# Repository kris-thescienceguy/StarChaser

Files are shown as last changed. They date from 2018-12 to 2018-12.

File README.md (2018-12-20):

# Star Chaser: Automatic Dome Controller

The Star Chaser dome control project was led by Kris Turner as part an upgrade, commissioned by Keele Observatory, in order to improve the functionality of their 24" research, reflector telescope.

Keele Observatory is located in North Staffordshire,  between Manchester and Birmingham on a large estate with extensive woods, lakes and parkland, formerly owned by the Sneyd family. 97% of the university's research is classified as world leading and of international importance, as a result of the 2014 Research Excellence Framework (REF 2014).

The software and digital electronics were produced by **Kris Turner**, who at the time of the project, was an undergraduate physics with chemistry student. The mechanical designs were produced by **Dr James Albinson**. **Alan Bagnell** advised on the design, and safety, of the electrical systems.

*A special mention must be made to the entirety of the Keele Observatory volunteers without who there would be no dome to upgrade.*

## Project Overview ##

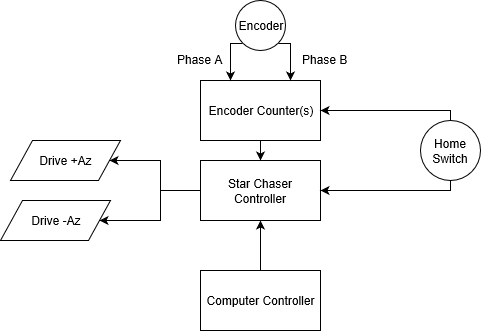
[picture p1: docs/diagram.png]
Schematic diagram of project


## Wiring Specifications ##
The system has several parts which may need to replaced over time so for ease of use a wiring colour chart has been produced. This should be used in conjunction with wiring diagrams provided.

### Pulse Switch ###
There is no doubt that the microcontroller will miss some encoder pulses. It may also count some twice. Whether by gain or loss of pulses it’s likely that with extended use and due to cumulative error the accuracy of the system will decrease over time. In order to prevent this, a zero point was chosen where the microcontroller knows the exact azimuth of the dome. Using a magnet on the dome structure and a fixed reed switch, a pulse is sent to the microcontroller when this zero point is reached.

On this interrupt, the microcontroller resets the pulses counted and hence the azimuth of the dome to a known position. This switch is also polled by the driver software as part of the AtHome subroutine.

| Switch Wire | Extended Cable |
| --- | --- |
| Red | Orange |
| Blue | Blue |

### Encoders ###
In order to accurately determine the position of the dome, two incremental encoders are used, although only one is required and currently configurd. Each encoder has four wires: VCC, GND, A Phase, and B Phase. Phase A and phase B are interchangable but will reverse the direction of the encoder. The encoder phase signals require an external pull-up resistor and although the ATTiny25 microcontroller provides internal pull-ups they do not appear to be strong enough.

#### Encoder A ####
| Encoder Function | Encoder Wire | Extended Cable |
| --- | --- | --- |
| VCC | Red | Orange |
| GND | Black | Blue |
| Phase A | Green | Green |
| Phase B | White | Brown |

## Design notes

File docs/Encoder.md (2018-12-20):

# Star Chaser: Automatic Dome Controller
## Encoder Circuit ##

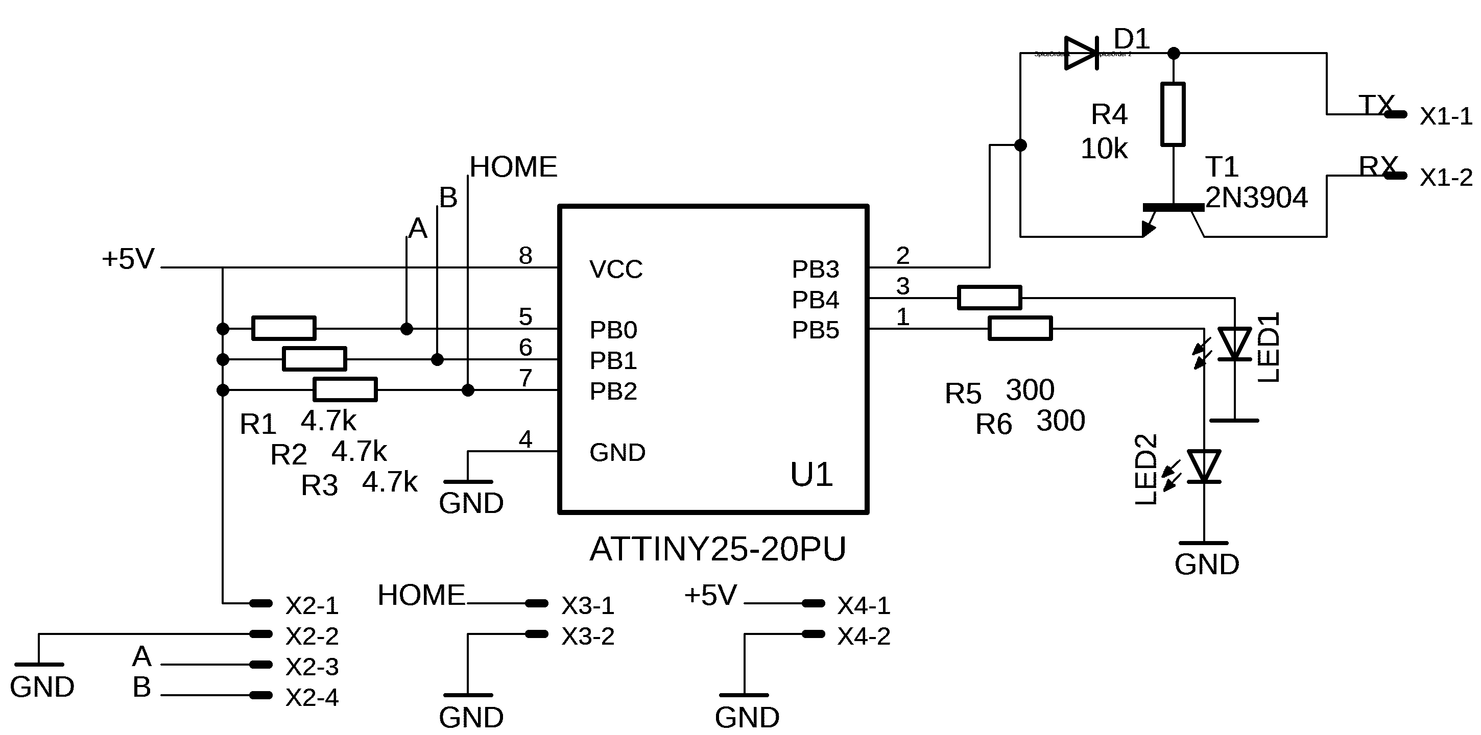
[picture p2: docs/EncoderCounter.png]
Electronic circuit schematic for counting encoder pulses


The encoder circuit is responsible for recording the two 90° out of phase pulses from the rotary encoder. The square waveform, shown below, is measured by the ATTiny25 pins P0 and P1.

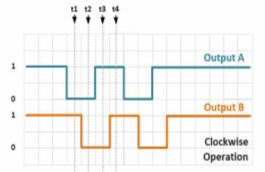
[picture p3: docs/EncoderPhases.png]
Electronic circuit schematic for counting encoder pulses


The encoder circuit is simple, but powerful due to its modular nature. The ATTiny25 is powered from a regulated 5V power bus. Each encoder phase is pulled up through a 4.7k resistor to 5V as is required by an open-collector encoder.

The pros and cons of this is discussed over at CUI Inc https://www.cui.com/blog/comparison-of-common-encoder-output-signals.

The third input, the home switch, is attached to P2 configured as an external interrupt. Again this pin is pulled high by a 4.7k resistor which is grounded by a reed switch in the presence of a magnetic field. This falling edge triggers an interrupt on the ATTiny25 which resets the pulse count to zero.

The board communicates with the controller chip using a software half-duplex serial UART based on a design by Ralph Doncaster which allows only one pin on the ATTiny to be used to both send and receive data. The library compiles to only 62 bytes of memory which is perfect due to the limited memory available on the microcontroller. A more indepth description of the circuit is available from http://nerdralph.blogspot.com/2014/01/avr-half-duplex-software-uart.html.

One status LED's indicate that the dome is moving as measured by the encoders.

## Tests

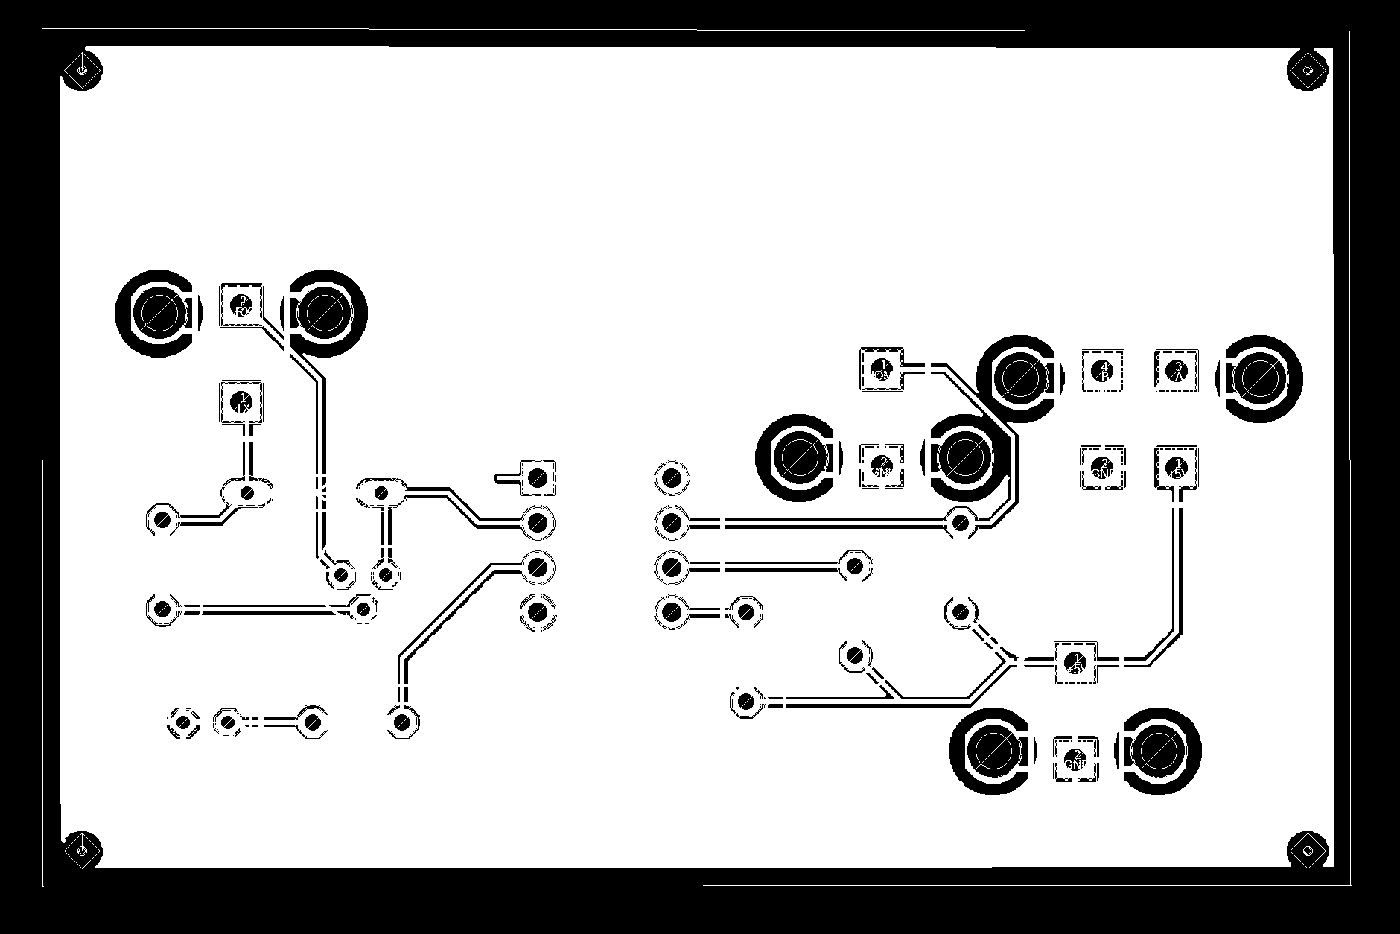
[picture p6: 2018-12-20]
Measurement/PCB.png

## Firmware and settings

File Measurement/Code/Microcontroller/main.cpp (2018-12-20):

/*
 * EEPROM_Dump.cpp
 *
 * Created: 18/12/2018 16:23:59
 * Author : krist
 */ 
#define F_CPU 1000000UL

#include <avr/io.h>
#include <util/delay.h>
#include <avr/interrupt.h>
#include "BasicSerial3.h"

/*
* Pin Definitions
*
* P0 Phase A
* P1 Phase B
* P2 Home
* P3 Serial
* P4 Movement LED
* P5 Reset
*
*/

const signed int encoderDirections[] = {0, -1, 1, 0, 1, 0, 0, -1, -1, 0, 0, 1, 0, 1, -1, 0};
volatile long encCount = 0;
volatile int noMovement = 0;

int main(void)
{
	DDRB = (1 << 3 ); // DDRB = 0011 1000
	PORTB |= (7 << 3); // Flash LEDs (sets P4 to pull up resistor)
	
	bool waitingForStartByte = true;
	
	while (waitingForStartByte){
		if (RxByte() == 's'){
			waitingForStartByte = false;
		}
	}
	
	PORTB &= (0 << 0); // PORTB = 0000 0000 to set pull up resistors off, and set all outputs to zero
	
	GIMSK |= (1 << 5);     // turns on pin change interrupts by setting bit 5 of GIMSK to 1
	GIMSK |= (1 << 6);   // turns on external interrupts
	PCMSK |= (3 << 0);   // set pin change interrupts on pins 0 and 1. Decimal 3 = Binary 11

	/*
	MCUCR Register: ISC0[1:0]: Interrupt Sense Control 0 Bit 1 and Bit 0
	0 0 The low level of INT0 generates an interrupt request.
	0 1 Any logical change on INT0 generates an interrupt request.
	1 0 The falling edge of INT0 generates an interrupt request. <=== This is what we want.
	1 1 The rising edge of INT0 generates an interrupt request.
	*/
	
	MCUCR |= (1 << 1);
	MCUCR &= ~(1 << 0);

	sei();                     // turn on interrupts

	
    /* Replace with your application code */
	
    while (1) 
    {
		//home = ((PINB >> 3) & 1); // Get state of home pin (shifts to LSB and then sets the rest of the array to 0)
		//encCount = encCount * home; // Home is default at 1 until pulled to ground by pin.
		noMovement += 1;
		
		if (noMovement > 5000){
			PORTB &= ~(1 << 4);	
		}
		
		// Transmit value out
		int numberOfBytes = (encCount / 255) + 1;
		for (int byteIndex = 0; byteIndex < numberOfBytes; byteIndex++)	{
			int shiftIndex = (numberOfBytes - byteIndex - 1)*8;
			int transmitByte = (encCount >> shiftIndex) & 255; // Ensures only first 8 bits have value
			TxByte(transmitByte);
		}
		TxByte('#');
    }
}

/* Pin Change Interrupts */
ISR (PCINT0_vect) {
	static unsigned int oldEncoderState = 0;
	
	oldEncoderState <<= 2;
	oldEncoderState |= (PINB & 0x03);
	encCount += encoderDirections[(oldEncoderState & 0x0F)];
	PORTB |= (1 << 4);
	noMovement = 0;

}

/* External Interrupt - takes priority */
ISR (INT0_vect) {
	noMovement = 0;
	PORTB |= (1 << 4);
	encCount = 0;	
}

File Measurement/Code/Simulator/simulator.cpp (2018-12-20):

/******************************************************************************

                              Online C++ Debugger.
               Code, Compile, Run and Debug C++ program online.
Write your code in this editor and press "Debug" button to debug it.

*******************************************************************************/

#include <iostream>
#include <bitset>
#include <fstream>

using namespace std;

const signed int encoderDirections[] = {0, -1, 1, 0, 1, 0, 0, -1, -1, 0, 0, 1, 0, 1, -1, 0};
volatile long encCount = 0;

int currentPins = 0;
int timeOfNoMove = 0;

int directionToMove(int oldEncoderState, int currentEncoder){

		cout << "Current State: " << bitset<2>(currentEncoder) << ". Old State: " << bitset<2>(oldEncoderState) << ". ";

        oldEncoderState <<= 2;
		oldEncoderState |= (currentEncoder & 0x03);
		int direction = encoderDirections[(oldEncoderState & 0x0F)];
		encCount += direction;
		
		cout << "Direction: " << direction << ". Total Position: " << encCount << "." << endl;

		//home = ((PINB >> 3) & 1); // Get state of home pin (shifts to LSB and then sets the rest of the array to 0)
		
		if (direction == 1) {
			//cout << "+AND " << ~(1 << 5); // Turns off -Az pin so that PORTB = XX0X XXXX
			currentPins &= ~(1 << 5);
			cout << "Current pins: " << bitset<8>(currentPins) << endl;
			//cout << "+OR " << (1 << 4) << endl;// Turns on +Az pin so that PORTB = XXX1 XXXX
			currentPins |= (1 << 4);
			cout << "Current pins: " << bitset<8>(currentPins) << endl;
		}else if(direction == -1){
			//cout << "-ANDS " << ~(1 << 4) << endl; // Turns off +Az pin so that PORTB = XX0X XXXX
			currentPins &= ~(1 << 4);
			cout << "Current pins: " << bitset<8>(currentPins) << endl;
			//cout << "-ORS " << (1 << 5) << endl; // Turns on -Az pin
			currentPins |= (1 << 5);
			cout << "Current pins: " << bitset<8>(currentPins) << endl;
		}else{
		    currentPins &= ~(3 << 4); // Turns off both +Az pin and -Az pin
			cout << "Something broke. Current pins: " << bitset<8>(currentPins) << endl;
		}
		
		return direction;
}


int main(void)
{
    /* Replace with your application code */
	static unsigned int oldEncoderState = 0;
	bool home = 0;
	int oldState = -10;

  	ifstream data ("simulator_tests/10rpm.txt", ifstream::in);
	ofstream output ("output.txt");

	int i = 0;
	//ofstream out ("simulator_tests/output.txt");
	if ( data.is_open() ) {
		int state;
		while ( data >> state ) {
			if (oldState == -10) { oldState = state; cout << "First run." << endl; continue;}
			directionToMove(oldState, state);
			oldState = state;
			int LED1 = ((currentPins >> 4) & 1);
			int LED2 = ((currentPins >> 5) & 1);
			output << i << " " << encCount << " " << LED1 << " " << LED2 << endl;
			i +=1;
		}
		data.close();
	}else{ cout << "Something went wrong" << endl; }
	
}

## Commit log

2018-12-15 Update README.md
    Wiring specifications were added.
2018-12-15 Added project schematic diagram.
2018-12-15 Added encoder counter circuit.
2018-12-17 Added details regarding to measurement of the encoder pulses.
    [measurement.brd, measurement.sch]
2018-12-20 Updated measurement circuit and uploaded. Needs reviewing and then ordering.
    [DataVisualiser.xlsx, measurement.brd, measurement.sch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]
2018-12-20 Encoder circuit document updated
